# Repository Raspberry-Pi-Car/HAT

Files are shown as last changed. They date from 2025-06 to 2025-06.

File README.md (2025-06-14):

# HAT
A custom PCB for adding sensors and hardware interfacing

# V4

## Connected Devices / GPIO Pins
### I2C
| Device | Usage | Documentation | 
| --- | --- |--- |
| ICM-20948 | 9-DoF Interial Measurement Unit (Accelerometer, Gyroscope, and Magnetometer) | [9-DoF IMU Datasheet](https://invensense.tdk.com/wp-content/uploads/2016/06/DS-000189-ICM-20948-v1.3.pdf)|
| PCA9685BS,118 | 16-Channel, 12-bit PWM Driver | [PWM Driver Datasheet](https://www.nxp.com/docs/en/data-sheet/PCA9685.pdf) |

### SPI
| Device | Usage | Documentation | 
| --- | --- |--- |
| MCP-3008  | Analog to digital converter | [MCP 3008 Datasheet](https://cdn-shop.adafruit.com/datasheets/MCP3008.pdf) |

## Connected GPIO pins

| Device | GPIO / Pin |
| --- | --- |
| Ultrasonic Trigger | GPIO22 / Pin 15 |
| Ultrasonic Echo | GPIO23 / Pin 16 |
| Switch | GPIO26 / Pin 37 |

## Device and Connector Description

Most connectors are JST PH, 40-pin to Raspberry Pi is a female 2x20 header. Long pins are optional for possible future expansion but are not necessary, an extended standard female GPIO interface can be used. 

On the JST connectors, pin 1 is closest to the dot or with the soldered tabs facing up, is on the right side.

Information below may be repetitive, designed to focus on either the connector view or the device view. 

#### Battery
| Pin | Connection | Description |
| --- | --- | --- |
| 1 | Battery (+) | Connected to main power switch (next to connector) |
| 2 | Battery (-) | Ground for PCB (GND) |

#### Motor A
| Pin | Connection | Description |
| --- | --- | --- |
| 1 | Motor Controller AOUT1 | (A-) side |
| 2 | Motor Controller AOUT2 | (A+) side |

#### Motor B
| Pin | Connection | Description |
| --- | --- | --- |
| 1 | Motor Controller BOUT2 | (B+) side |
| 2 | Motor Controller BOUT1 | (B-) side |

#### AD0/1 POT
| Pin | Connection | Description |
| --- | --- | --- |
| 1 | +5V | Power |
| 2 | AD0 | Voltage divider (ground side) with POT0 |
| 3 | AD1 | Voltage divider (ground side) with POT1 |
| 4 | GND | Ground |

#### AD2/3
| Pin | Connection | Description |
| --- | --- | --- |
| 1 | +5V | Power |
| 2 | AD2 | For motor encoder |
| 3 | AD3 | For motor encoder |
| 4 | GND | Ground |

#### AD4/5
| Pin | Connection | Description |
| --- | --- | --- |
| 1 | +5V | Power |
| 2 | AD4 | For motor encoder |
| 3 | AD5 | For motor encoder |
| 4 | GND | Ground |

#### Ultrasonic
| Pin | Connection | Description |
| --- | --- | --- |
| 1 | +5V | Power |
| 2 | GPIO22 / Pin 15 | Trigger pin for the ultrasonic Sensor |
| 3 | GPIO23 / Pin 16 | Echo pin for ultrasonic Sensor (though a 2/3 voltage divider)
| 4 | GND | Ground |

#### I2C
| Pin | Connection | Description |
| --- | --- | --- |
| 1 | +5V | Power |
| 2 | GPIO2 SDA | SDA I2C line 1 |
| 3 | GPIO3 SCL | SCL I2C line 1 |
| 4 | GND | Ground |

### Motor Controller

The motor controller (DRV8411) can drive up to two brushed dc motors at up to 2A each. The inputs and controls are described below. The direction, forward and reverse, are relative to the motor do not necessarily mean the direction of motion of the vehicle.

| Connector | Connection |
| --- | --- |
| JST MotorA | AOUT1 [Pin 2] and AOUT2 [Pin 1] |
| JST MotorB | BOUT1 [Pin 2] and BOUT2 [Pin 1] |

| PCA 9685 Channel | Motor Controller input | Motor Controller Out | Controller Behavior |
| --- | --- | --- |
| 12 |  AIN1  | AOUT1 | A reverse (A- to A+) |
| 13 |  AIN2  | AOUT2 | A forward (A+ to A-) |
| 14 |  BIN2  | BOUT2 | B reverse (B- to B+) |
| 15 |  BIN1  | BOUT1 | B forward (B+ to B-) |

The motor controller works by driving the motor in the direction that has the high signal. If multiple inputs are enables at the same time the motor controller will appear to take the difference of the two signals but will draw more power.

| IN1 | IN2 | Behavior |
| ----- | --- | --- |
| LOW | LOW | High Z / Coast |
| HIGH | LOW | OUT1 -> OUT2 (Forward) |
| LOW | HIGH | OUT2 -> OUT2 (Reverse) |
| HIGH | HIGH | Brake |

### AD Converter

| AD input | Usage |
| --- | --- |
| 0 | Voltage divider (ground side) with POT0 |
| 1 | Voltage divider (ground side) with POT1 |
| 2 | Pin 2 (left middle) on connector AD2/3  for motor encoder |
| 3 | Pin 3 (right middle) on connector AD2/3 for motor encoder |
| 4 | Pin 2 (left middle) on connector AD4/5  for motor encoder |
| 5 | Pin 3 (right middle) on connector AD4/5 for motor encoder |
| 6 | Not connected |
| 7 | Not connected |

### IMU
The ICM20498 is used as the Inertial Movement Unit on board. It has 9-way capability allowing for x, y, and z-axis capture of Acceleration, G-Force, and Magnetic Headings. This device communicates view the I2C bus and has no other external connections. 

## 2x20 Pin Header (GPIO)

| PIN # | Usage | 
| --- | --- |
| 1 | Raspberry Pi 3.3V | 
| 2 | Raspberry Pi 5V | 
| 3 | I2C Data Line 1 (See I2C Devices) | 
| 4 | Raspberry Pi 5V | 
| 5 | GPOIO 03:I2C Clock Line 1 (See I2C Devices)  | 
| 6 | Raspberry Pi GND  | 
| 7 | GPIO 4: GPCLCK  | 
| 8 | GPIO 14: UART TX (Transmit Data)  | 
| 9 | Raspberry Pi GND  | 
| 10 |  GPIO 15: UART RX (Receive Data)  | 
| 11 |  GPIO 17:Alert pin for INA260. Programmable Pin for detecting under/over voltage/current | 
| 12 |  GPIO 18: PWM0  | 
| 13 |  GPIO 27: Unused  | 
| 14 |  Raspberry Pi GND  | 
| 15 |  GPIO 22: Unused | 
| 16 |  GPIO 23: Unused | 
| 17 |  Raspberry Pi 3.3V | 
| 18 |  GPIO 24: Unused | 
| 19 |  GPIO 10: Master Out Slave In (MOSI) for MCP3008 and added SPI devices | 
| 20 |  Raspberry Pi GND | 
| 21 |  GPOIO 09: Master Input Slave Output (MISO) for MCP3008 and added SPI devices | 
| 22 |  GPIO 25: Unused | 
| 23 |  GPIO 11: Serial Clock (SCLK) for MCP3008 and added SPI devices | 
| 24 |  GPIO 08: Chip Enable 0 (SPI0 CE0) for MCP3008 and added SPI devices | 
| 25 |  Raspberry Pi GND | 
| 26 |  GPIO 07: Chip Enable 1 (SPI0 CE1)  | 
| 27 |  GPIO 00: I2C Data Line 0 (no I2C devices using currently)  | 
| 28 |  GPIO 01: I2C Clock Line 0 (no I2C devices using currently) | 
| 29 |  GPOIO 05: Unused | 
| 30 |  Raspberry Pi GND | 
| 31 |  GPIO 06: Unused | 
| 32 |  GPIO 12: PWM0 | 
| 33 |  GPIO 13: PWM1 | 
| 34 |  Raspberry Pi Ground | 
| 35 |  GPIO 19: GPIO Switch | 
| 36 |  GPIO16: Unused | 
| 37 |  GPOIO 36: H Drive Fault detection  | 
| 38 |  GPIO 20: UltraSonic Sensor Trigger  | 
| 39 |  Raspberry Pi GND | 
| 40 |  GPIO 21: UltraSonic Sensor Echo |

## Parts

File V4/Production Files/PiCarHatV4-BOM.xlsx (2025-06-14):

Comment | Description | Designator | Footprint | LibRef | Quantity | Part Number | P&P Comment | JLCPCB Part #
100nF | 50V 100nF X7R ±10% 0805 Multilayer Ceramic Capacitors MLCC - SMD/SMT ROHS | C1, C3, C10, C11, C14, C15, C17 | FP-CC0805-0_85-IPC_B | CMP-2100-03606-3 | 7 | CC0805KRX7R9BB104 |  | C1711
10uF | 25V 10uF X5R ±10% 0805 Multilayer Ceramic Capacitors MLCC - SMD/SMT ROHS | C2, C12 | FP-GRM21B-0_15-MFG | CMP-2007-03541-2 | 2 | GRM21BR61E106KA73L |  | C15850
220uF | 220uF 10V 90mA@120Hz ±20% SMD, D6.3xL5.4mm Aluminum Electrolytic Capacitors - SMD ROHS | C8 | RVT1A221M0605-Footprint-1 | CMP-001-00090-1 | 1 | RVT1A221M0605 |  | C3345
10nF | 50V 10nF X7R ±10% 0805 Multilayer Ceramic Capacitors MLCC - SMD/SMT ROHS | C9 | CAPC2013X100X50NL20T25 | CMP-2007-03708-1 | 1 | C0805F103K5RACTU |  | C1710
1uF | 50V 1uF X7R ±10% 0805 Multilayer Ceramic Capacitors MLCC - SMD/SMT ROHS | C13 | CAPC2013X140X50LL20T25 | CMP-2007-03234-1 | 1 | C0805C105K3RACTU |  | C28323
100uF | 100uF 16V 63mA@120Hz ±20% SMD, D6.3xL5.4mm Aluminum Electrolytic Capacitors - SMD ROHS | C16 | RVT1C101M0605-Footprint-1 | CMP-001-00087-2 | 1 | RVT1C101M0605 |  | C37308
SS34 | 40V Independent Type 3A 550mV@3A SMA(DO-214AC) Schottky Diodes ROHS | D1 | SS34-Footprint-1 | CMP-004-00033-3 | 1 | SS34 |  | C8678
5-103817-2 | 2.54mm Pin Headers ROHS=Gold 1kV 3A Direct Insert Policy 2.5mm 260℃ 3mm 12P -40℃~+105℃ 6mm 2.54mm Triple row Brass 3x4P Plugin,P=2.54mm Pin Headers ROHS=2.54mm Pin Headers ROHS | J1, J7 | TE_5-103817-2 | CMP-023-000000-3 | 2 | TSW-104-07-L-T |  | C32713291
2.54-2*20P--PC104 | 2.54mm 2.54mm Double Row 40P Brass Direct Insert 2x20P Plugin,P=2.54mm Female Headers ROHS | J2 | New footprint 1 | CMP-002-00076-7 | 1 | 2.54-2*20P母长PC104 |  | C35165
B4B-PH-SM4-TB(LF)(SN) | 2.0mm pitch/Disconnectable Insulation displacement and Crimp style connectors | J3, J4, J5, J6, J8 | FP-B4B-PH-SM4-TB-MFG | CMP-002-00074-1 | 5 | B4B-PH-SM4-TB(LF)(SN) |  | C160354
B2B-PH-SM4-TB(LF)(SN) | 1x2P 2P PH Tin 2 -25℃~+85℃ 2A 1 2mm Brass Alloy Standing paste SMD,P=2mm Wire To Board Connector ROHS | J9, J10, J11 | FP-B2B-PH-SM4-TB_LF_SN-MFG | CMP-002-00073-1 | 3 | B2B-PH-SM4-TB |  | C160352
FXL1050-470-M | 3.7A 47uH Integrated molded inductor ±20% 4.5A SMD,10x11.5mm Power Inductors ROHS | L1 | FXL1050-470-M-Footprint-1 | CMP-006-00021-2 | 1 | FXL1050-470-M |  | C5359268
KT-0603R | -40℃~+85℃ Red 0603 LED Indication - Discrete ROHS | LED1, LED2, LED3, LED4, LED5 | XL-1608SURC-06-Footprint-1 | CMP-007-00038-5 | 5 | KT-0603R |  | C2286
Mounting Hole (2.7/6 mm) | DO NOT PLACE | PTH1, PTH2, PTH3, PTH4 | New footprint 1 | CMP-00030-00001-4 | 4 |  | NO NOT PLACE
3.74k | 100mW Thick Film Resistors 75V ±100ppm/℃ ±1% 3.74kΩ 0603 Chip Resistor - Surface Mount ROHS | R1 | RESC1608X55X30LL15T15 | CMP-2000-00466-1 | 1 | ERJ-3EKF3741V |  | C137728
36k | 100mW Thick Film Resistors 75V ±100ppm/℃ ±1% 36kΩ 0603 Chip Resistor - Surface Mount ROHS | R3 | RESC1608X55X30LL20T20 | CMP-2000-00046-1 | 1 | ERA3AEB363V |  | C23147
2k | 100mW Thick Film Resistors 75V ±100ppm/℃ ±1% 2kΩ 0603 Chip Resistor - Surface Mount ROHS | R4, R5, R16, R24 | RESC1608X55X25LL10T15 | CMP-2000-06937-1 | 4 | RC0603FR-072KL |  | C22975
27k | 100mW Thick Film Resistors 75V ±100ppm/℃ ±1% 27kΩ 0603 Chip Resistor - Surface Mount ROHS | R6 | RESC1608X55X25LL10T15 | CMP-2000-06933-1 | 1 | RC0603FR-0727KL |  | C22967
3k | 100mW Thick Film Resistors 75V ±100ppm/℃ ±1% 3kΩ 0603 Chip Resistor - Surface Mount ROHS | R7, R8, R9 | RESC1608X55X25LL10T15 | CMP-2000-04040-1 | 3 | RC0603FR-073KL |  | C4211
33k | 100mW Thick Film Resistors 75V ±100ppm/℃ ±1% 33kΩ 0603 Chip Resistor - Surface Mount ROHS | R10 | RESC1608X55X25LL10T15 | CMP-2000-06938-1 | 1 | RC0603FR-0733KL |  | C4216
18k | 100mW Thick Film Resistors 75V ±100ppm/℃ ±1% 18kΩ 0603 Chip Resistor - Surface Mount ROHS | R11, R12 | RESC1608X55X30LL15T15 | CMP-1012-00650-3 | 2 | ERJ3EKF1802V |  | C25810
1.13k | 100mW Thick Film Resistors 75V ±100ppm/℃ ±1% 1.13kΩ 0603 Chip Resistor - Surface Mount ROHS | R13, R23 | RESC1609X50X30LL10T20 | CMP-2000-02979-1 | 2 | CRCW06031K13FKEA |  | C137782
4D03WGJ0103T5E | 4 ±5% 10kΩ 62.5mW ±200ppm/℃ 0603x4 Resistor Networks, Arrays ROHS | RN1 | 4D03WGJ0103T5E-Footprint-1 | CMP-009-00177-2 | 1 | 4D03WGJ0103T5E |  | C29718
4D03WGJ0101T5E | 4 ±5% 100Ω 62.5mW ±200ppm/℃ 0603x4 Resistor Networks, Arrays ROHS | RN2, RN3, RN4 | 4D03WGJ0101T5E-Footprint-1 | CMP-009-00185-2 | 3 | 4D03WGJ0101T5E |  | C25506
SS-12M11G3 | Horizontal Plug 6A Single Pole Double Throw (SPDT) 120V 120V 6A 10000 times Black Plugin Slide Switches ROHS | S1 | SS-12M11G5-Footprint-1 | CMP-011-00018-2 | 1 | SS-12M11G3 |  | C2879832
K3-1235D-K1 | 300mA Direct Insert Single Pole Double Throw (SPDT) 6V 10,000 times Black Plugin Slide Switches ROHS | S2 | K3-1235D-K1-Footprint-1 | CMP-011-00015-2 | 1 | K3-1235D-K1 |  | C145860
DRV8411PWPR | Motor/Motion/Ignition Controllers & Drivers 1.65-V to 11-V, 4-A, dual H-bridge motor driver with current regulation 16-HTSSOP -40 to 125 | U1 | PWP0016C-IPC_B | CMP-00024-00008-1 | 1 | DRV8411PWPR |  | C18212622
LM324QT | Operational Amplifier, 4 Func, 9000uV Offset-Max, BIPolar, PQCC16 | U2 | LM324QT-Footprint-1 | CMP-014-00002-6 | 1 | LM324QT |  | C183029
LM2596S-ADJ(UMW) | Step-down type Adjustable 40V 1.2V~37V 3A TO-263-5 DC-DC Converters ROHS | U3 | TS5B_L | CMP-0069-00272-2 | 1 | LM2596S-ADJ(UMW) |  | C347423
TL431ASA-7 | 2.495V~36V ±1% 100mA Adjustable SOT-23 Voltage Reference ROHS | U8 | FP-SOT23-MFG | CMP-12755-000001-1 | 1 | TL431ASA-7 |  | C145101
PCA9685PW,118 | IC LED DRIVER RGBA 28-TSSOP | U12 | FP-SOT361-1-IPC_B | CMP-1595-00003-3 | 1 | PCA9685PW,118 |  | C2678753
ICM-20948 | Accelerometer and Gyroscope Compass 9-Axis Digital 24-Pin QFN T/R | U14 | TDK-QFN-24_L | CMP-031-00007-7 | 1 | ICM-20948 |  | C726001
TPS79318DBVR | 200mA 70dB Fixed 1.8V Positive electrode 5.5V SOT-23-5 Voltage Regulators - Linear, Low Drop Out (LDO) Regulators ROHS | U15 | DBV0005A_M | CMP-0394-00328-2 | 1 | TPS79318DBVR |  | C7102
MCP3008-I/SL | 2.7V 4-Channel/8-Channel 10-Bit A/D Converters with SPI Serial Interface, 16-Pin SOIC 150mil, Industrial Temperature | U18 | SOIC-SL16_L | CMP-0188-00041-2 | 1
3362P-1-103LF | ±10% ±100ppm/℃ 500mW 10kΩ Plugin-3P,7x6.6mm Potentiometers, Variable Resistors ROHS | VR1, VR2 | BOUR-3362P | CMP-00001-1 | 2 | 3362P-1-103LF |  | C58159

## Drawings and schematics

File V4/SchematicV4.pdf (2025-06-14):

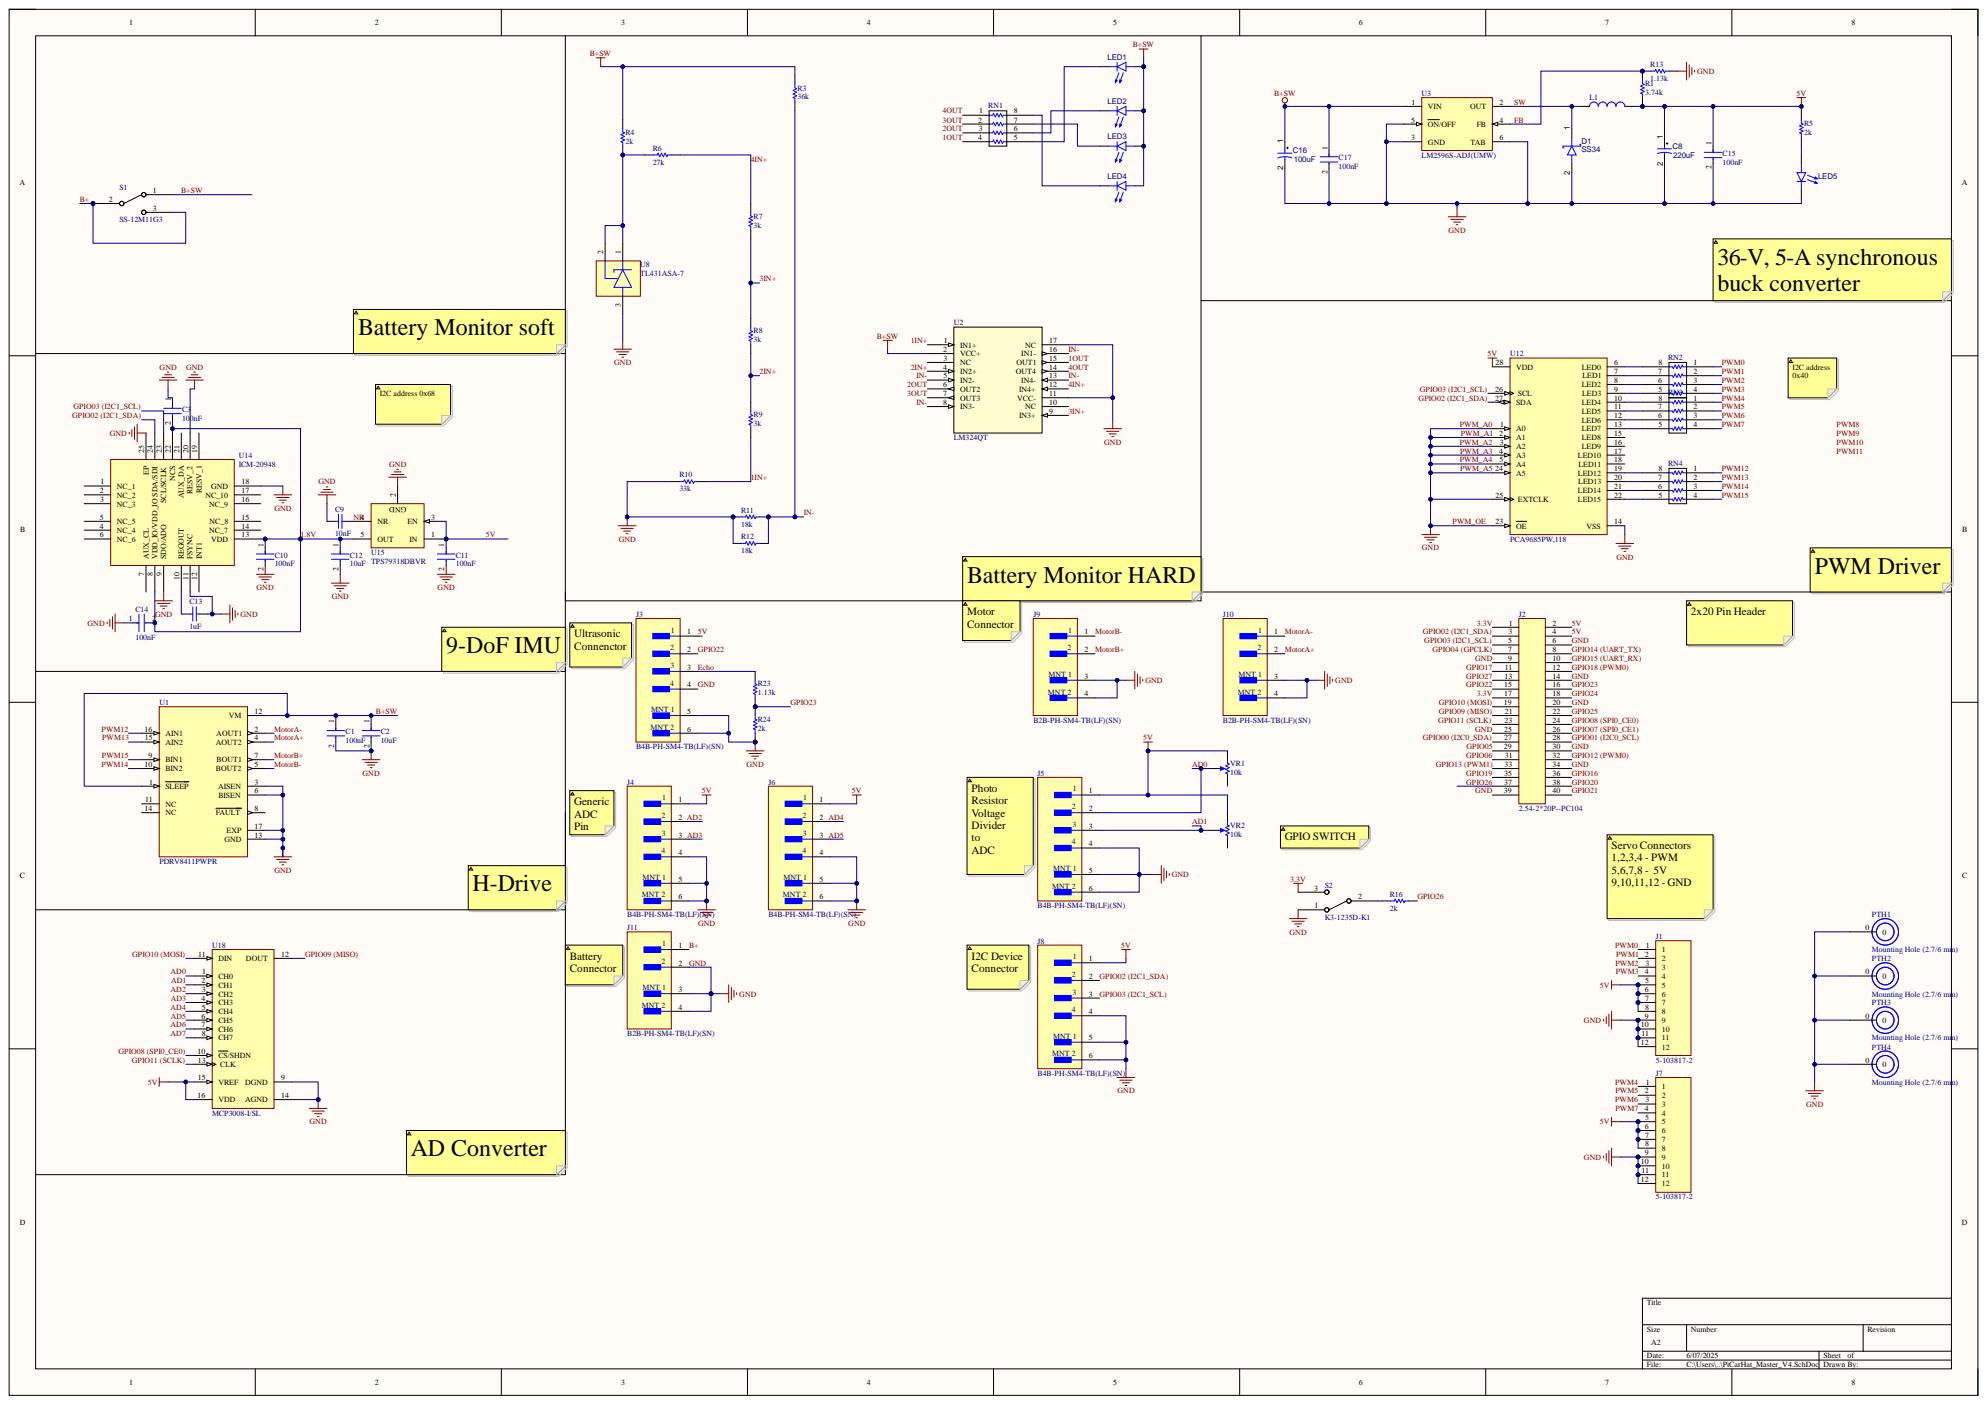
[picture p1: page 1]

ON/OFF 5

RESV_1 19 RESV_2 20 AUX_DA 21 NCS 22 SCL/SCLK 23 SDA/SDI 24 EP 25

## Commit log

2025-05-07 Update README.md
    I2C and SPI pins updated... gpio coming later
2025-05-07 Update README.md
    added 2x20 Pin header with GPIO descriptions
2025-05-07 Added Altium Schematic and PCB documents
    [PiCarHat_Master_V2.SchDoc]
2025-06-14 updated Readme and updated the production files
    [PiCarHatV4-BOM.xlsx, PiCarHatV4.PrjPcb, PiCarHat_Master_V4.SchDoc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]
